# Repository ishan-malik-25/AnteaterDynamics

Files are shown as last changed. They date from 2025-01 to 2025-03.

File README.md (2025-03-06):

# Anteater Dynamics 7DOF Robot Blog

Welcome to our GitHub Page! We are a team of six undergraduate engineers working with our industry sponsor ROBOTIS to develop a 
7-degree-of-freedom robotic arm to be used by robotics enthusiasts and to help in data collection to be used to 
further develop robotics systems. This page will document our team's progress throughout the lifespan of our project
and will include any files, simulations, documents, or other relevant information pertaining to our project.

Team members:

Rogel Aguilar - Mechanical Engineering Major, Software Subteam - https://www.linkedin.com/in/rogelagui/

Diego Avila - Mechanical Engineering Major, Software Subteam

Lucas Cardona - Mechanical Engineering Major, Mechanical Subteam - https://www.linkedin.com/in/lucas-cardona/

Noah Castillo - Mechanical Engineering Major, Electrical Subteam - https://www.linkedin.com/in/noahscastillo/

Ishan Malik - Mechanical Engineering Major, Mechanical Subteam - https://www.linkedin.com/in/ishanmalik1/

Tomas Mejia - Mechanical Engineering Major, Electrical Subteam 

----------------------------------------------------------------------------------------------------------------------------------
Update 3/6/2025 - Mechanical Subteam

This week has been focused on developing a proof of concept to be displayed at our university's winter design review on March 13th. 
For this design review, mainly for the sake of simplicity, and since our software is still being developed, we are splitting the arm assembly
into two separate parts. Both of these components now have updated CAD models and bill of materials that include all of the fasteners
necessary for assembly. We have also obtained all of the actuators and frames from ROBOTIS, and are in the process of 3D printing
all of the necessary components to assemble our proof of concept in the next coming week.

First will be the end effector with the load cells, where focus will be calibrating the load cells and
gaining an understanding of how the torque applied to the servo on the end effector translates to a certain value of gripping force. All parts for the end efffector have been manufactured and are assembled, once the load cells are calibrated we can begin testing this subsystem.



End Effector parts that were manufactured.

Second is the arm linkage, which is simplified into a 4-DOF arm without an end effector, so we can focus on understanding how 
various servo inputs translate into positioning the arm into a desired orientation. Our focus with the linkage arm will be on
repeatability of achieving desired positions, and will include attaching masses to the end of the linkage to analyze how
adding mass affects the accuracy and repeatability of the arm's movement. 



Arm Linkage to be Shown at Design Review, Simplified into 4DOF with Fasteners

As the project progresses into our next academic quarter, the focus will be on fully integrating the entire assembly and making the
system as a whole looks more polished, with shrouds and covers for cables and servo joins similar to those implemented on the 
Open Manipulator X platform.

CAD assembly files of both the proof of concept assemblies will be uploaded to this repository as well as the updated BOMs for these parts.
We have also included a copy of the preliminary testing plan for our proof of concept, which may evolve as we start assembling components.

----------------------------------------------------------------------------------------------------------------------------------
Update 2/27/2025

This week was focused on each of our team members completing an individual component analysis for a part in the robotic arm.
All of these analysis reports are uploaded to this repository to be viewed. These analyses helped justify the design decisions
made in our engineering design process.

Additionally, we made our project poster to be shown at our school's Winter Design Review on March 13th. This poster
summarizes the project and has also been uploaded to this repository.

----------------------------------------------------------------------------------------------------------------------------------

Update 2/20/2025 - Noah

FEA on our custom end effector brackets has been completed. We were discussing manufacturing materials for custom components and had considered either 1060 Aluminum or ABS plastic. The project's intention is to design the robot for at-home manufacturing as well as mass production, and thus want to emphasize additive manufacturing technologies. However, we were concerned that certain connecting components may need a stronger aluminum material to handle the loads. However, the simulation results show that a simple ABS plastic is structurally sound even under a 2X scaled load. In the simulation, the bracket assembly is subjected to a 12 N force acting on the four bracket screw holes. Using aluminum, the maximum displacement is only 0.00063 mm, and for ABS the maximum displacement is 0.022955 mm. Such a small displacement, even using ABS, has proven that using ABS plastic is sufficient for our custom bracket.



Displacement Results of Bracket Assembly using ABS



Displacement Results of Bracket Assembly using 1060 Aluminum

Update 2/20/2025 - Ishan

More progress has been made on the CAD, mainly on the base design - changing it from a simple circular plate to a more realistic
final design. See the picture below. Also finite element analysis (FEA) work has begun to optomize the shape of the linkage arms to
resist bending, I have also attached a few images of FEA results for the original linkage arm cross section seen in the previous
CAD models as well as one for an H-Beam. More shape iterations are currently in progress.


New Base first Revision - Packaging of RB-150 and Base Servo, Holes for Bolting/Clamping


Original Cross Section FEA Displacement with 2N Point Force Applied


H-Beam FEA Displacement Results with 2N Point Force Applied 

----------------------------------------------------------------------------------------------------------------------------------

UPDATE 2/10/2025 - Ishan

More progress has been made on the CAD (RevC) as we are finalizing the selection of the Dynamixel X servos being used in our arm. 
We were having trouble balancing the 7DOF functionality desire with the budget we are targeting and as such have changed some of the
servos used. Previously, all of the servos were from the XM line, but we had to change this to incorporating servos from the 
XC, XM, and XL lines to balance our cost and functionality requirements. We also changed the last servo in the linkage from two
separate servos to a single 2-axis XC-430 servo to save both cost and weight at the end of the linkage. An updated CAD model can
be seen below. The pink servos are XC-430, the green servo is XM-430, the orange is XL-430, and the light blue is the 2-axis 2XL-430.
Additionally, we have uploaded a copy of our project problem definition presentation to the site to be viewed!


Robotic Arm RevC

Dynamixel X Servo Decision Matrix

----------------------------------------------------------------------------------------------------------------------------------
UPDATE 2/4/2025 - Ishan

Progress has been made on the CAD! See the attached photos. The assembly now uses all ROBOTIS actuators and frames.
The servos in the assembly are not specified as they will be in the final assembly as calculations need to be done to ensure
that stall torques are not achieved on any servos. The ROBOTIS form factors for the servos are all ROBOTIS 430 dimensions except for the base 
servo which is 540 dimensions. The overall reach of the arm is now ~655mm, but this can be adjusted by varying the length of the links 
once more robot kinematics are further validated. The arm as shown in the picture has 6 degrees of freedom, with one degree of
freedom reserved for the end effector that is still being developed. Link cross-sections are also yet to be optimized. This
will be done in the coming weeks using FEA once the lengths are more final, so we know what types of forces and moments are 
being experienced by the links on the arm. Note this is Revision B of the CAD; Revision A did exist between the preliminary CAD
and RevB but was mostly used to integrate ROBOTIS servos and frames, while RevB is more representative of our project objectives.



Robotic Arm RevB



Overall Arm Reach at Current Revision

----------------------------------------------------------------------------------------------------------------------------------

1/29/2025



Preliminary Linkage

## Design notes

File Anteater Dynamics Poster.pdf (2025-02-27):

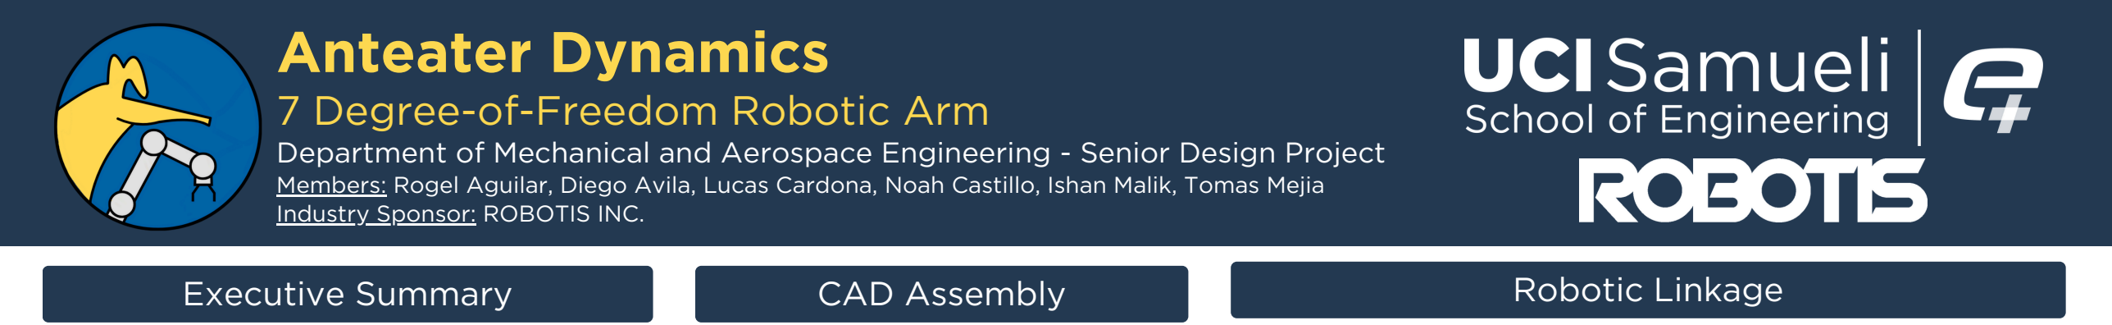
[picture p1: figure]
Robotic Linkage; CAD Assembly; Executive Summary; Anteater Dynamics 7 Degree-of-Freedom Robotic Arm; Industry Sponsor: ROBOTIS INC.
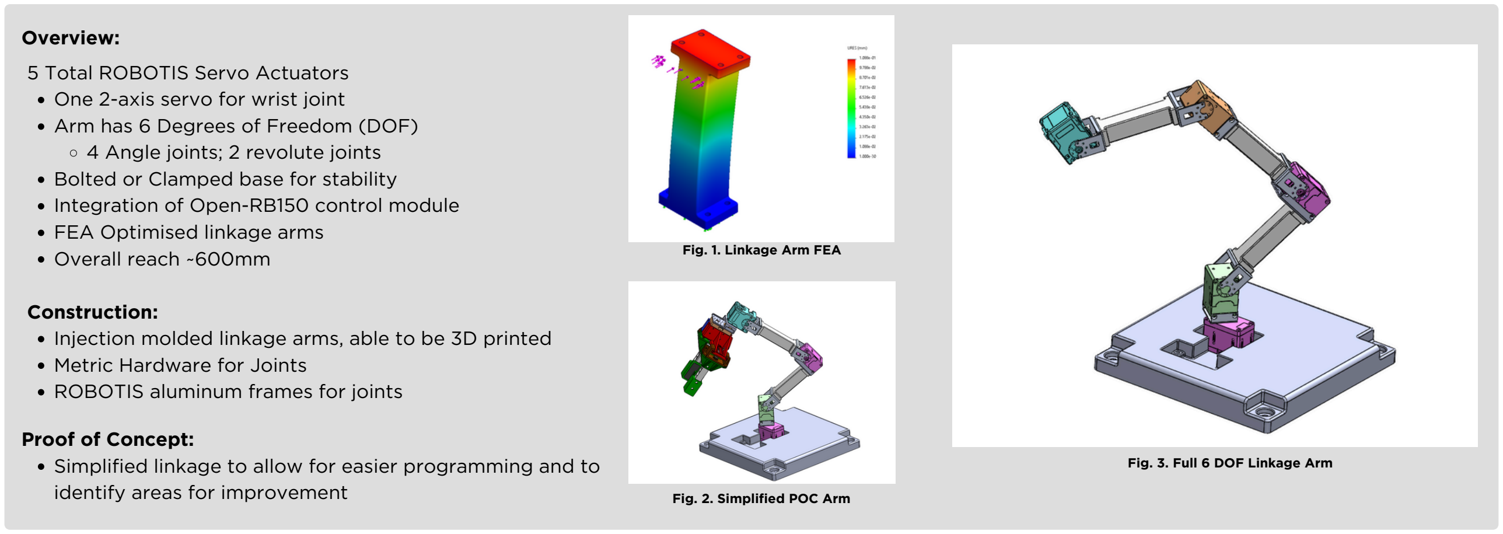
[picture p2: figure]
Overview:; 5 Total ROBOTIS Servo Actuators One 2-axis servo for wrist joint Arm has 6 Degrees of Freedom (DOF) 4 Angle joints; 2 revolute joints Bolted or Clamped base for stability Integration of Open-RB150 control module FEA Optimised linkage arms Overall reach ~600mm; Construction:; Metric Hardware for Joints ROBOTIS aluminum frames for joints; Proof of Concept:; identify areas for improvement; Fig. 1. Linkage Arm FEA; Fig. 2. Simplified POC Arm; Fig. 3. Full 6 DOF Linkage Arm

# End Effector

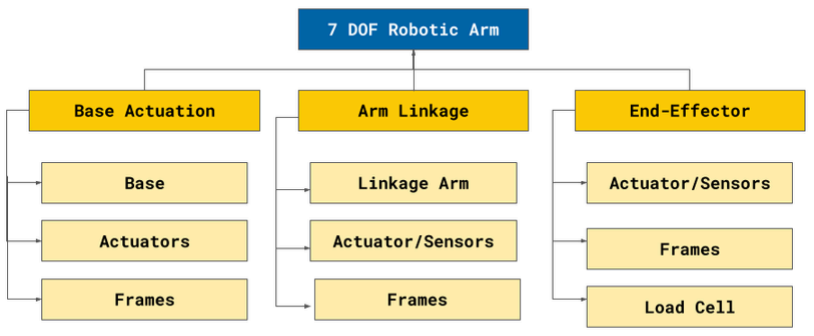
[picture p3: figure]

(A) Base Actuator
FRA-1: The base actuator shall rotate 360 degrees to pick up objects around it
FRA-2 The base shall provide a stable and secure mounting platform for the arm linkage FRA-3 The base shall support the mass of the robot and a load of 400g at the end effector
(B) Arm Linkage
FRB-1: The arm linkage shall provide the reach to pick objects at a distance of 500mm away FRB-2: The servos in the arm linkage shall support the load of 400g at the end effector FRB-3 The arm linkage shall articulate to move around obstructions
(C) End Effector
FRC-1: The end effector shall pick up small household objects
FRC-2: The end effector shall sense gripping forces
FRC-3: The end effector shall be able to grip the expected loads of 400g

# Functional Requirements

The current machine learning research landscape is utilizing robotic systems to collect data on which AI models are trained. Companies such as our industry sponsor, ROBOTIS Inc., provide at-home robotics kits for enthusiasts to collect data and train AI models. The problem is that the available consumer options are either low budget, robot kits with low fidelity or high-end kits that may be unrealistic for many consumers.
Anteater Dynamics seeks to bridge the gap between existing market options by developing a mid-range robotic system capable of 7 degrees of freedom with integrated load sensors to collect critical data for AI training. Our solution is open-source, priced around $1000, and designed for additive manufacturing, allowing consumers to either purchase full kits from ROBOTIS Inc., or opt to manufacture their robot independently from any hobbyist 3D printer. The system is also designed to integrate ROBOTIS Inc. proprietary electronics for optimized linkage kinematics. Simulated kinematic analysis validates unrestricted 7DOF movement and if the 4DOF prototype demonstrates the system effectiveness, the Anteater Dynamics robotic arm could provide the robotics machine learning community with a robust and capable solution for AI training.

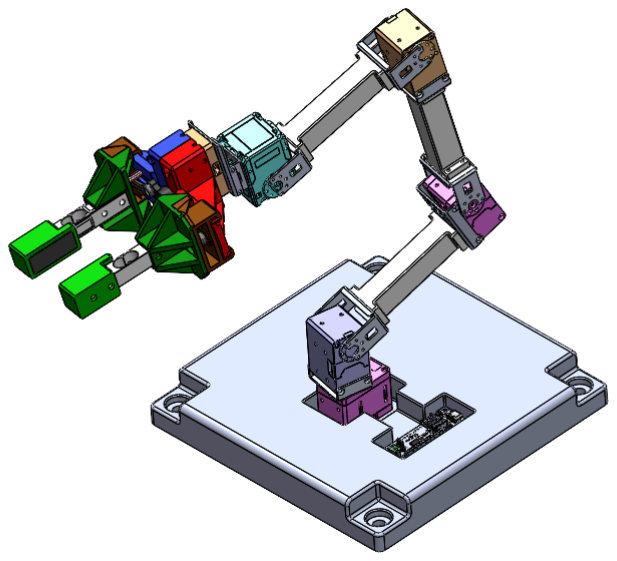
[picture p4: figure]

# Existing Solutions

# Future Improvements

# References and Awknowledgements

Our team would like to thank our sponsor ROBOTIS, for providing feedback and guidance, as well as supplying Anteater Dynamics with DYNAMIXEL servos and other ROBOTIS components. We would also like to thank our MAE151A instructors, Professors David Copp and Mark Walter, and our TA Abdelrahman ElMaradny.

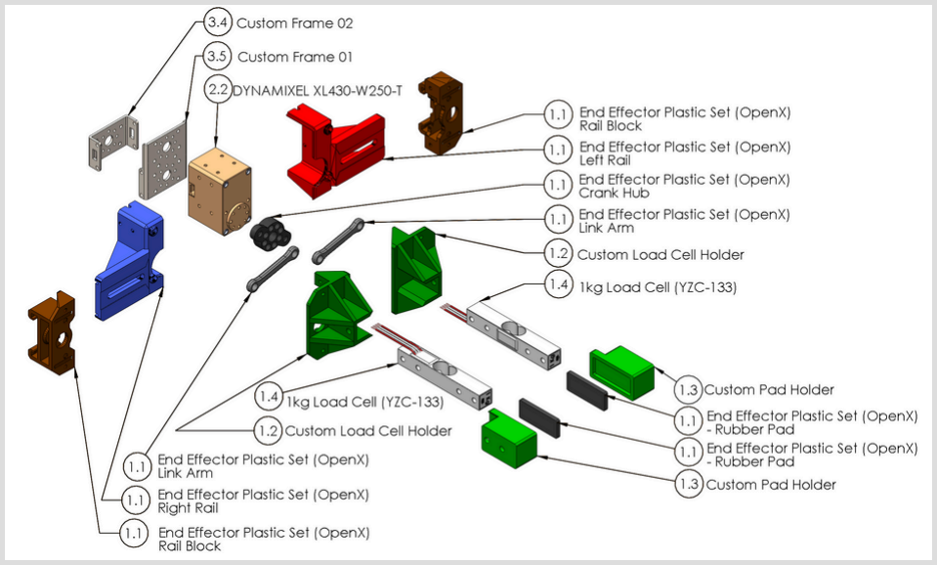
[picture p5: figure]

# Controls/Software

# Structural Decomposition

# Department of Mechanical and Aerospace Engineering - Senior Design Project

Members: Rogel Aguilar, Diego Avila, Lucas Cardona, Noah Castillo, Ishan Malik, Tomas Mejia

O Assembled & Exploded Views: verview: ROBOTIS XL430-W250-T Actuator
- Max Jaw Width; 50.5mm
Construction;
- Injection Molding
- 3D Printing
Active Grip Control;
Each “finger” of the claw is equipped with a 1kg Load Cell. Allowing for machine learning to actively control its applied grip force.
Modularity;
Fingertip pads can be easily swapped for specific
applications.
Fig. 5. End Effector - Assembled View Right Fig 6. End Effector - Exploded View

Fig. 4. End Effector - Assembled View Left

Pseudocode Flowchart

AI Integration and Control

Interchangeable end effectors

Shortcomings | For the Future

Servo Torque Control

Expensive Servos

Torque requirements

Servo Optimization

Complex Control Algorithms

Injection molded linkage arms, able to be 3D printed

Simplified linkage to allow for easier programming and to

Fig 1. Koch v1.1 Robot Arm $237
Low Fidelity
4 DOF

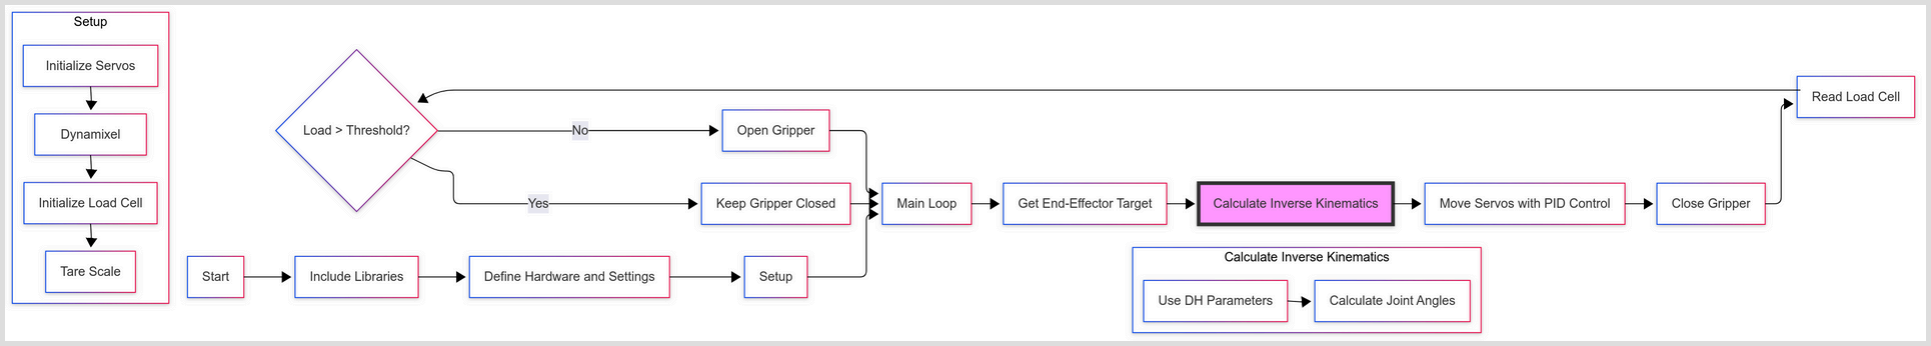
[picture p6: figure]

Fig 7. Flowchart of the Robotic Controls Code

Fig 2. OpenManipulator-X Robot Arm $1,416
High Fidelity
6DOF

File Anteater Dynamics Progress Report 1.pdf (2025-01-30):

# Anteater Dynamics 7 DOF Robot

01/23/2025 - 01/30/2025

Rogel Aguilar, Diego Avila, Lucas Cardona, Noah Castillo, Ishan Malik, Tomas Mejia
University of California, Irvine Henry Samueli School of Engineering

# Summary

Over this past week, Anteater Dynamics primarily focused on operational tasks. The team developed a contract that our members are meant to follow over the project lifespan. The team is currently working on problem definition, gaining an understanding of what specific components and needs must be integrated into the system. Additionally, a basic linkage design was created in Solidworks, validating the number of degrees of freedom and getting a basic understanding of the kinematics of the robotic arm.

https://github.com/ishan-malik-25/AnteaterDynamics

# Goals

Goal 1: Kinematic validation of robotic arm with 7DOF

Goal 2: Developed problem definition for project objectives

# Outcomes

Goal 1: Kinematics Validation

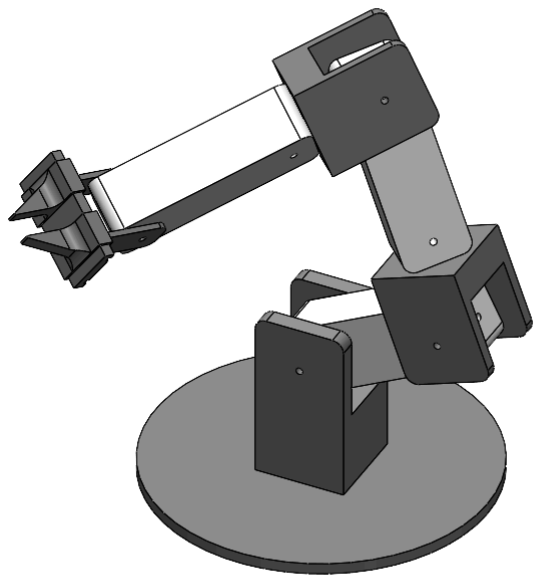
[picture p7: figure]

- Kinematics mock-up of 7DOF robotic arm in Solidworks

Goal 2: Problem Definition

Problem Defenition (https://docs.google.com/presentation/d/1wHaiUMOAIBBrATz0K1sZ1rZ3FSAhI8pwVjJIr-QNW-A/edit?usp=sharing)
- Problem Definition presentation is in progress

# Moving Forward

Plans before the next reporting period include refining and performing simulations to verify our kinematic outline further. The Mechanical sub-team will take the lead in the outline, while the other team members will provide support and feedback.

The electrical team will continue to finalize the actuators and other components needed to transition from modeling and simulation to physical prototyping.

The software team will begin to set deadlines and objectives to familiarize themselves with the ROS and Gazebo software environment.

We anticipate encountering challenges in any initial simulations especially as we continue to refine and clarify our design requirements and needs. The concept generation stage for our kinematic outline will require a lot of back-and-forth between the teams so we need to take into consideration the time needed to spend on the project.

# Time Tracking

1/24 (3 hours, ALL)--Completing Sponsorship Interview Summary
Teammates collaborated on summarizing key takeaways from the initial sponsor interview last Thursday

1/27 (1.5 hours, ALL)--Completing Team Contract
Teammates collaborated on establishing norms on how the team will function going forward. An organizational chart was established and individual design roles were assigned.

1/28 (1.5 hours, ALL)--Existing Solution Research and Preliminary BOM prep
During our lab time, we explored existing robotic arms to start thinking about how we could approach the problem. Additionally, system needs and requirements started to be brainstormed

1/29 (1.5 hours, ALL )--Problem Definition, Timeline creation, Public Documentation During our lab time, more work was done on our problem definition. A Gantt Chart was started to track the team’s group and individual tracks. The type of public documentation was decided, and a GitHub Page was created

1/29 (2 hours, Ishan)--Preliminary Linkage CAD
Preliminary design of our CAD model was developed by Ishan with input from the team.

Link to Gantt Chart (https://docs.google.com/spreadsheets/d/15tDmBBRLZHagoX_M0EPwx-CAiR3B7cbavoiCkAHe7NM/edit?usp=sharing)
Link to GitHub (https://github.com/ishan-malik-25/AnteaterDynamics)

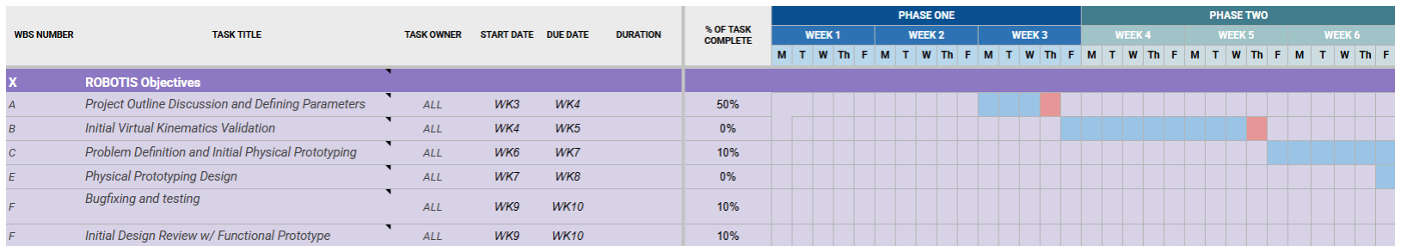
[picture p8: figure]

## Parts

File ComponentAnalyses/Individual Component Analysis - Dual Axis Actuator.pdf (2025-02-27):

Individual Component Analysis – Dual Axis Actuator

Project Description

This project’s objective is to design and manufacture a robotic arm with seven degrees of freedom. The goal is to give consumers a more affordable yet quality robot arm that can be utilized to collect data for machine learning and artificial intelligence.

Analyzed Component: DYNAMIXEL 2XL430-W250-T

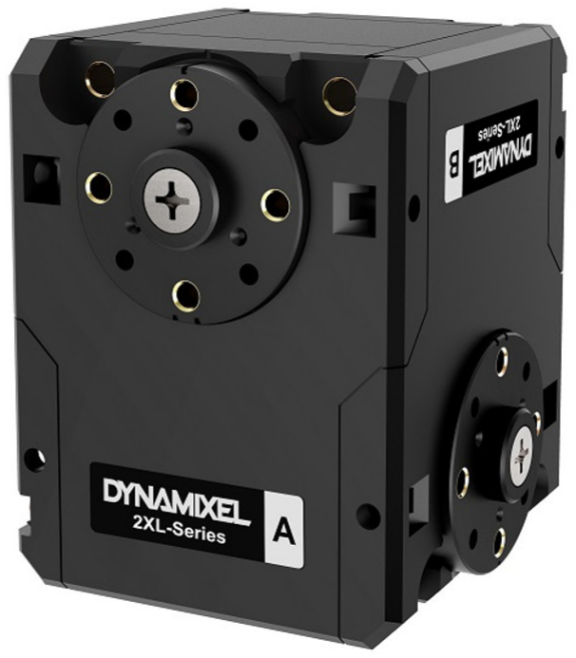
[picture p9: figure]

Figure 1: DYNAMIXEL 2XL430-W250-T
The component that will be analyzed in this write-up is the DYNAMIXEL 2XL430-W250-T, a dual axis actuator sold by Robotis. This component is critical to the design because it serves as the connection between the robot’s arm linkage and end effector. It also provides an additional two axes giving the end effector a wider range of mobility and flexibility.

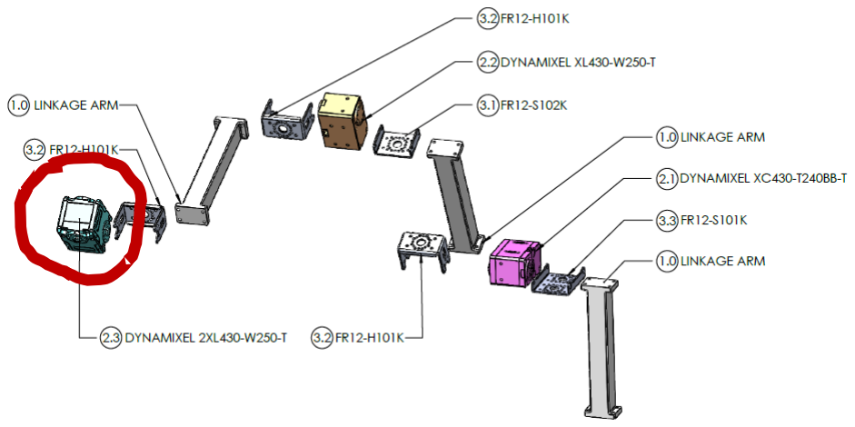
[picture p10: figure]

Figure 2: The DYNAMIXEL 2XL430-W250-T is the final component on the arm linkage and is what is used to join it and the end effector
Functional Requirements
Requirement Code | Requirement
FR-001 | The actuator shall be capable of supporting the end effector
FR-002 | The actuator shall be capable of lifting a load of 500 grams when grabbed by the end effector
FR-003 | The actuator shall be dual axis or utilize two actuators for two degrees of freedom

Component Options

The project’s sponsor set a requirement that all actuators were to be Robotis brand. This meant options were limited to their catalogue. The following is a short description of three alternate options to the DYNAMIXEL 2XL430-W250-T.

DYNAMIXEL 2XC430-W250-T:

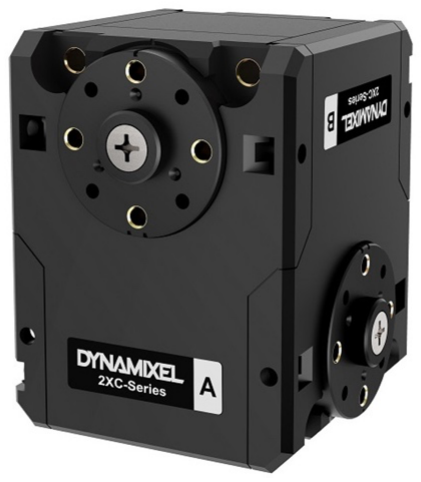
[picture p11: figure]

The 2XC430-W250-T is a dual axis actuator with a 1.8nm stall torque.

DYNAMIXEL XL430-W250-T:

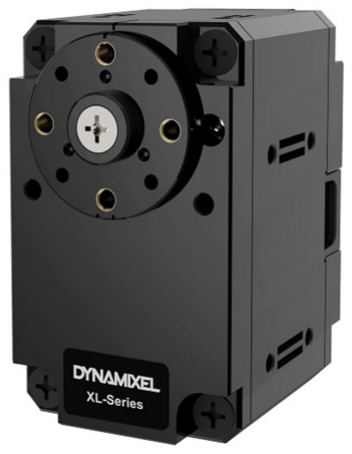
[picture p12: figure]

The XL430-W250-T is a single axis actuator with a 1.4nm stall torque. Two in junction are required to achieve an equivalent number of degrees of freedom.

DYNAMIXEL XL330-M288-T:

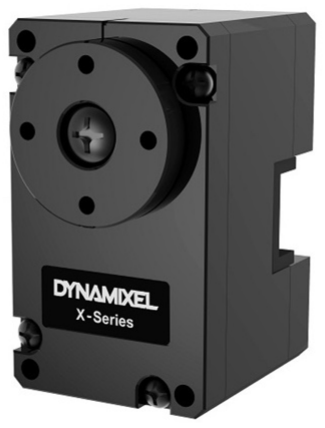
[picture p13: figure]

The XL330-M288-T is a single axis actuator with a 0.52nm stall torque. Two in junction are required to achieve an equivalent number of degrees of freedom

Summary Table

Component Name | Cost | Pros | Cons
2XL430-W250-T. | $129.90 | • Dual Axis • Inexpensive • Good torque • Metal Gears | • Large
2XC430-W250-T | $259.90 | • Dual Axis • High torque • Metal gears | • Large • Expensive
XL430-W250-T | $49.90 | • Inexpensive • Good torque | • Single Axis • Plastic gears
XL330-M288-T | $23.90 | • Inexpensive • Small and light | • Single Axis • Low torque • 5V input

Component Justification

The reason for selecting the 2XL430-W250-T is primarily for its dual axis operation, cost and for having a good stall torque.

Dual axis capabilities play a big role for the actuator selection. It is desirable to have two axes for the end effector because it gives it additional movement and rotation for it to pick up objects. Besides the 2XL430-W250-T, the 2XC430-W250-T is the only other dual axis actuator that Robotis sells. It has a stronger motor with a stall torque of 1.8nm over the 1.4nm of the 2XL. The major drawback to it, however, is that it is double the cost. Additionally, the XC series of actuators are praised for their more durable metal gears, however, the 2XL is also equipped with metal gears. The twice as large price tag is unjustifiable because its only standout attribute over the 2XL is its higher stall torque. Because this actuator is placed right before the end effector, the moment on the motors is not as large, especially compared to those closer to the base, so the additional torque isn’t weighted as strongly. For the alternate single axis options, to achieve the save mobility as the dual axis, two actuators connected are required. This adds additional complexity and cost for required hardware. In addition, the total weight and size of two actuators generates a larger moment for the actuators at the base.

As stated before, the cost of the 2XC is unjustifiable for the little benefits it provides. The XL430 and XL330 are both cheaper options but requiring two doubles their cost. Using two motors, the XL330 still shows to be an affordable option. Looking deeper at its low stall torque of 0.52nm, it is roughly a third of the stall torque the 2XL, making it a less competitive option. Doing rough calculations, the motor needs at least 1nm of torque to fulfill the lifting capacity of 500grams for the project. The 2XC capable of 1.5nm of torque surpasses this target making it the clear choice of actuator.

Specifications

Weight: 98.2g

No-load RPM: 57 RPM

Dimensions: 36x46.5x36mm

Resolution: 4096 steps

Voltage Input: 11.1V

Stall Current

Stall Torque

Gear Ratio: 257.4:1

Dual Axis

References

Sutyasadi, Petrus. Control Improvement of Low-Cost Cast Aluminium Robotic ..., repository.usd.ac.id/45285/1/9057_11+Control+Improvement+of+Low-Cost+Cast+Aluminium+Robotic+Arm+Using+Arduino+Based+Computed+Torque+Contr ol.pdf. Accessed 8 Dec. 2022.

2XL430-W250 ..., https://emanual.robotis.com/docs/en/dxl/x/2xl430-w250/

2XC430-W250 ..., https://emanual.robotis.com/docs/en/dxc/x/2xc430-w250/

XL430-W250 ..., https://emanual.robotis.com/docs/en/dxl/x/xl430-w250/

XL330-M288-T ..., https://emanual.robotis.com/docs/en/dxl/x/xl330-m288/

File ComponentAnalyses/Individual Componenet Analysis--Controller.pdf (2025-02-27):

# Individual Component Analysis: Controller

## 1. Project Description and Individual Component Justification

Anteater Dynamics is working on a low-cost 7 degree-of-freedom robotic arm using proprietary components supplied by the team’s industry sponsor ROBOTIS Inc. The motivation behind the project was for hobbyists and robotics enthusiasts to have a middle ground between low-fidelity budget options and cost prohibitive high-fidelity options. One of the main requirements for this project is to keep the total cost under $1000. Below is a grey box diagram of the major functions the robotic system aims to achieve.

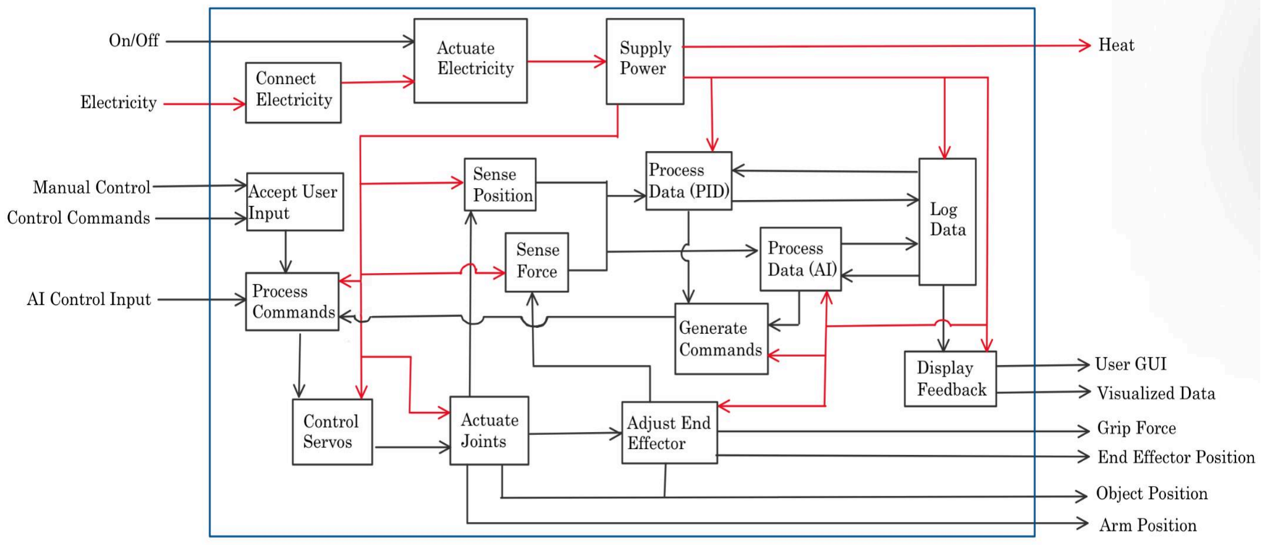
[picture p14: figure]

Fig 1. Grey Box Diagram of the Robotic Arm [1] The controller plays in integral role as this component will receive the manual control and control commands from the user, and process those commands to help achieve the final end effector position through mathematical computation (inverse kinematics), adjust the grip force of the end effector by reading load cell data, as well as displaying data through a GUI. The type of controller is critical as it needs to be able to handle executing all the different functions described in the grey box diagram shown above.

## 2. Functional Requirements and Other Considerations

The functional requirements of the robotic controller are as follows:
FR-Cr1: The controller shall control six servos at once
FR-Cr2: The controller shall be able to perform mathematical calculations such as forward or inverse kinematics
FR-Cr3: The controller shall process input data from the load cells

While not necessarily requirements there are other considerations and suggestions that should be taken into account. The end-product is aimed toward hobbyists and other robotic enthusiasts as well as researchers. With this broad end-user audience, the controller should be relatively simple to use, or should not have too high of a learning curve. Additionally, cost shall be considered when choosing a controller as the main goal of this project is to keep the final product price to be under $1000.

## 3. Concepts or Options

From the DYNAMIXEL quick start manual and selection guide, the DYNAMIXEL servos can be controlled three ways, by an Arduino-compatible microcontroller, a single-board computer (SBC), or directly from a PC. [2, 3] For this component the three options will be
1. A generic Windows or macOS laptop with at least 8 GB of RAM.
2. A Raspberry Pi 4 Model B (2 GB RAM) SBC.
3. The OpenRB-150 controller.

For direct PC control, the specifications for the PC will be based on the Lenovo IdeaPad Slim 3i 15.6" available at Costco [4]. This is a newer generation of a laptop currently used by a project member and can operate a variety of different applications including WSL, SolidWorks, and MATLAB. Control of the DYNAMIXEL servos can be achieved via the DYNAMIXEL Software Development Kit (SDK) which allows the DYNAMIXEL to be programmed in several different languages. A diagram of how the PC is connected to the DYNAMIXEL is shown in the figure below.

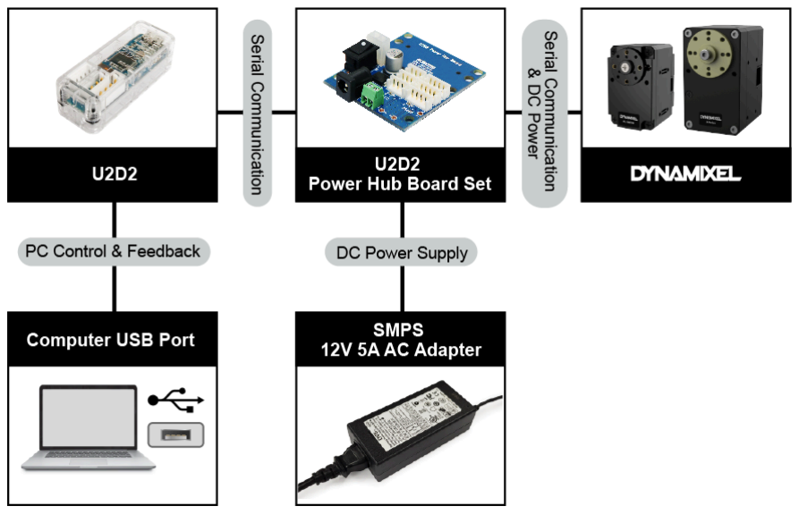
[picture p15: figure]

Figure 2. Flowchart highlighting how a PC is connected to the the DYNAMIXEL servos [3]

As seen in the figure, three additional components are necessary for communication between the PC and the servos. The U2D2 converts USB to either TTL and/or RS-485, depending on which model servo is being used. The U2D2 power hub is what connects directly to the DYNAMIXEL and is connected to an external power source.

The Raspberry Pi 4 Model B is an SBC that runs on the Linux operating system. Similar to direct control from a PC, the Raspberry Pi can program the DYNAMIXEL through the Dynamixel SDK, and the flowchart shown in Figure 2. But instead of a Computer USB port, the Raspberry Pi USB port will be used.

Lastly, the OpenRB-150 is an Arduino-compatible microcontroller designed and sold by ROBOTIS. Control of the DYNAMIXEL servos can be achieved through the Arduino IDE and the Dynamixel Arduino library.

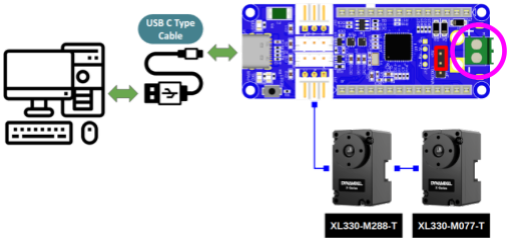
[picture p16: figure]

Fig 3. Diagram of OpenRB-150 Connection [3] As shown in figure above, the OpenRB-150 is the only component needed to control the robotic arm. Note that the OpenRB-150 can be powered through an external source via the pins circled in bright pink. This functionality is needed when using more powerful servos.

## 4. Pros and Cons Summary

Below is a table representing a summary of the pros and cons of the three different options:

Component | Pros | Cons
Direct PC | Most Versatile | High learning curve
| Highest Computing Capacity | Not Beginner Friendly
Raspberry Pi | Portable | Most Costly Solution
| Strong computing capability | Not beginner friendly

Limited Versatility compared to PC

OpenRB-150 | Arduino-compatible (beginner friendly) | Small memory/Weak computing power
| Cheapest Option | Only 4 TTL Ports

Only uses TTL ports

Highlighted in green is the chosen component. Further analysis how this decision was made will be discussed in the following section

## 5. Analysis and Justification

Rating 1-5 | Robotic Arm Controller
Direct PC | Raspberry Pi 4 B | OpenRB-150
Objectives | WEIGHT | Rating | Weighted Score | Rating | Weighted Score | Rating | Weighted Score
Cost | 40.00% | 3.00 | 24.00% | 1.00 | 8.00% | 5.00 | 40.00%
Computing Power | 30.00% | 5.00 | 30.00% | 4.00 | 24.00% | 1.00 | 6.00%
Compatibility/ Versatility | 15.00% | 5.00 | 15.00% | 3.00 | 9.00% | 1.00 | 3.00%
Ease of use | 15.00% | 3.00 | 9.00% | 2.00 | 6.00% | 4.00 | 12.00%
SCORES | 100.00% | 3.90 | 78.00% | 2.35 | 47.00% | 3.05 | 61.00%

The objectives listed in the weighted decision matrix relate to the functional requirements and other considerations discussed in section 2 of this paper. Important to note, an assumption was made that the end-user will already have a PC with similar or better specifications as the Lenovo laptop used in this analysis.
Cost is weighted as the most important factor as the goal of the project is to have a low-cost option for consumers. The OpenRB-150 gets the highest rate in this category, with a single board costing only $24.90. [5] The runner up is the direct PC control–under the assumption the user already has a PC similar in specifications to a Lenovo laptop–as the U2D2 starter pack costs $59.70 [6]. Under this assumption the direct PC controller received the rating of 3, since the cost of this method will only be the U2D2 and its accompanying Power Hub Board. The Raspberry Pi is the costliest option with an additional $44.99 for the SBC itself on top of the $59.70 cost of the U2D2 starter set [7]
Computing power is the second highest-weighted category. All the functional requirements require ample computing power and the direct control of the PC provides sufficient computing power to perform more resource intensive tasks such as calculating the proper thetas for rotation with inverse kinematics, or getting the final position of the end effector with forward kinematics. The Raspberry Pi 4 is the second highest-rated in computing power technology. As an SBC, the Raspberry Pi has a CPU which can process more data than an Arduino [8].
The next two categories carry the same weight, compatibility/versatility and ease of use. Compatibility and versatility is related to which languages and programming environments can be used in the controller. Again the PC had the highest rating since it can use all the languages supported by the Dynamixel SDK (C, C++, C-Sharp, Python, Java, Matlab, Labview, and ROS). [2, 3] While the Raspberry Pi 4 is able to use these languages as well, compatibility is limited for example, since MATLAB cannot be directly installed on and run on a Raspberry Pi. [9] Ease of use relates to how beginner friendly each controller is. While not a functional requirement, it’s important to consider given the large end-user audience. The OpenRb-150 has the highest rating here since the DYNAMIXEL can only be used in the ArduinoIDE environment along with the Arduino2Dynamixel library. These limitations help beginners code basic commands to the DYNAMIXEL servos.

## Specifications for Chosen Component

From the Decision Matrix, direct PC control is the chosen method for controlling the robot. The specifications for this component will be focused on the U2D2 and U2D2 Power Hub Interface devices.

The U2D2 connects to the PC via a USB Type-A cable. The ports on the U2D2 include a 3 Pin TTL and a 4 PIN RS-485, both for connecting to DYNAMIXEL. The last port is a 4 Pin UART. The maximum baud rate is 6 Mbps. [9]

The U2D2 Power hub has 3 TTL ports and 3 RS-485 to connect to the DYNAMIXEL servos. The U2D2 power hub has an operating voltage of between 3.5V and 24.0 V, with a max current of 10.0A.

## References and Notes

[1] Cardona, L., "Problem Definition," MAE 151A, PowerPoint presentation, Irvine, CA, Feb. 4, 2025. Slide 11
[2] “DYNAMIXEL Selection Guide,” ROBOTIS e-Manual, Mar. 24, 2024. https://emanual.robotis.com/docs/en/reference/dxl-selection-guide/#controller--interface (accessed Feb. 27, 2025).
[2] “DYNAMIXEL Quick Start Guide,” ROBOTIS e-manual, 2025. https://emanual.robotis.com/docs/en/dxl/dxl-quick-start-guide/ (accessed Feb. 27, 2025).
[3] “Lenovo IdeaPad Slim 3i 15.6" Touchscreen Laptop - Intel Core 5 120U - 1080p - Windows 11,” Costco Wholesale, 2022. https://www.costco.com/lenovo-ideapad-slim-3i-156-touchscreen-laptop---intel-core-5-120u---10 80p---windows-11.product.4000260119.html (accessed Feb. 27, 2025).
[4] “OpenRB-150,” ROBOTIS, 2025. https://www.robotis.us/openrb-150/ (accessed Feb. 27, 2025).
[5] “DYNAMIXEL Starter Set [US],” ROBOTIS, 2025. https://www.robotis.us/dynamixel-starter-set-us/ (accessed Feb. 27, 2025).
[6] “Raspberry Pi 4 Model B - 2GB DDR4,” Micro Center. https://www.microcenter.com/product/621439/raspberry-pi-4-model-b---2gb-ddr4?src=raspberry pi
[7] J. Cicolani and Springerlink (Online Service, Beginning Robotics with Raspberry Pi and Arduino : Using Python and OpenCV. Berkeley, Ca: Apress, 2018. Available: https://learning.oreilly.com/library/view/beginning-robotics-with/9781484268919/
[8] “Raspberry Pi,” Mathworks.com, 2024. https://www.mathworks.com/hardware-support/raspberry-pi.html (accessed Feb. 27, 2025).
[9] Y. Name, “U2D2,” ROBOTIS e-Manual. https://emanual.robotis.com/docs/en/parts/interface/u2d2/
[10] Y. Name, “U2D2 Power Hub,” ROBOTIS e-Manual. https://emanual.robotis.com/docs/en/parts/interface/u2d2_power_hub/

DYNAMIXEL Selection Guide (https://emanual.robotis.com/docs/en/reference/dxl-selection-guide/#controller--interface)
Direct PC/SBC:
- Requires U2D2
- Converts USB to TTL/RS-485 Signal
- Then the U2D2 Power Hub Board Set
- This also applies to when using the Raspberry Pi
- Power Supply

OpenRB-150:
- Needs an arduino or for our case OpenRB-150
- Power Supply

- Arduino IDE
- 4 TTL connectors

Software Tools:
- Dynamixel Wizard 2.0
- Works on both u2d2 and OpenRB [Source] (https://emanual.robotis.com/docs/en/parts/controller/openrb-150/)
- Dynamixel SDK (software development kit)
- Supports a lot of different languages
- Available on all three major OS (Linux, macOS, Windows
- Arduino Library
- ROBOTIS has library to make coding in arduino ide easier

DYNAMIXEL SDK Guide: (https://emanual.robotis.com/docs/en/software/dynamixel/dynamixel_sdk/overview/)
- Can be used for both PCs and SBC
- Can use these languages: C, C++, C#, Python, Java, MATLAB and LabVIEW

Costs (based on the ROBOTIS Website)

Direct PC:
- U2D2 starter set (https://www.robotis.us/dynamixel-starter-set-us/) is $59.70
- This will be the only cost for direct PC control
- If you do a la carte the u2d2 will cost 32.10
- The power hub will be 19.00
- 51.10 if bought a la carte

Raspberry Pi 4 Model B:
- U2D2 and then on top of that the actual raspberry pi
- From Micro-center (https://www.microcenter.com/product/621439/raspberry-pi-4-model-b---2gb-ddr4?src=raspberrypi) it will cost 44.99

OpenRB-150 (https://www.robotis.us/openrb-150/)
- Open RB itself will cost $24.90
Specs:
- 256 KB Flash Memory
- 32 KB SRAM

Can take both power from PC or external power supply

Quick pros and cons
OpenRB-150 is the CHEAPEST Option (Maybe put this in a decision matrix) OpenRB-150 is also most limiting since it can only be coded in arduino IDE

Raspberry pi:
More powerful than openrb-150 when it comes to computing (has better specs) Most Costly, assuming user has access to a laptop

PC:
Most versatility, can use a variety of different software programming tools
Least portable of the three. Potentially limiting as well if people don’t have access to a PC (say they only have a chromebook)

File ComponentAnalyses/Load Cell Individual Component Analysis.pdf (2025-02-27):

Lucas Cardona
Professor Walter
ENGRMAE 151A
Feb. 26, 2025
Individual Component Analysis; Load Cell
Description:
The 7 Degree of Freedom (7 DoF) Robotic Arm must be able to receive feedback data in regards to how much grip force it is applying at the end effector. Therefore, the design must include some sensor with the ability to detect the applied force on the object. This verifies a need for selecting an appropriate type of sensor and for this design a bar load cell was chosen. The bar style load cell is advantageous to the design as it can function as part of the “fingers” saving on the amount of needed plastic for injection molding. This being considered, the main requirements for the load cell are that it must be able to withstand the forces needed for holding a 400g object, have an overall length exceeding 45mm, and have an accuracy of +/- 0.1g or better.

Essential Qualities of Load Cells:
- Force sensing:
- Ensuring the robotic arm applies the correct force when grasping objects.
- Closed-loop control:
- Enabling feedback mechanisms for improved accuracy and responsiveness.
- Safety compliance:
- Preventing overloading or excessive force application that could damage components or objects.

Functional Requirements:
Label | Description | Justification
FR-3.1 | Withstand the force of holding a 400g object. | Being able to hold up and manipulate a 500g object is a requirement of our project. Therefore the load cell must be able to withstand the force necessary to do this.
FR-3.2 | Overall length at or exceeding 45mm | The original grippers of a previous ROBOTIS design are near 50mm, in order for the plastic savings to be advantageous the load cell must make up most of this distance.
FR-3.3 | Accuracy of +/-0.1g or better | In order for the feedback system to function the machine learning algorithm must be given accurate data. This will improve the overall performance of the end effector as well as allow a wider variety of objects to be manipulated.

Selected Options:
500G Load Cell (TAL221): | 1kg Load Cell (YZC-133): | 5kg Load Cell (YZC-133):


Overview: | Overview: | Overview:
- Length: 45mm | - Length: 80mm | - Length: 80mm
- Overload Capacity: 1000g | - Overload Capacity: 1500g | - Overload Capacity: 7500g
- Accuracy: 0.7 +/- 0.15 mV/V | - Accuracy: 1.0 +/- 0.15 mV/V | - Accuracy: 1.0 +/- 0.15 mV/V

All 3 options of the compared load cells use strain gauges to measure deformation in the bar. This specific method of measuring applied force is advantageous for our application because they offer high precision and reliability when compared to other options. These are essential qualities for ensuring our end effector can precisely know how much force it is applying and understand the object it is holding. Additionally, strain gauge load cells are very cost-effective allowing our project to remain under budget and be cheap to service. Different bar style load cells were also selected because much of the intended length for the end effectors claws will come from the body of the cell. A few drawbacks of these specific types of load cells are that they require amplification and can be susceptible to temperature variation. In our application temperature variation will not be much of a concern as the working environment will be a desktop. The need for an additional amplifier will affect our overall budget, however they are also cost-effective (~$10/piece).

Weighted Component Matrix:


Summary Table:
Component | Price | Pros | Cons
1kg Bar Load Cell (YZC-133) | $4.99 per unit | - 80mm in length - Appropriate range for application | - Lower safe overload percentage
5kg Bar Load Cell (YZC-133) | $4.99 per unit | - 80mm in length - Wide range of measurement | - Low accuracy - Lower safe overload percentage
500g Load Cell (TAL221) | $11.25 per unit | - Higher safe overload percentage - 150% Rated Load | - Sub-par length - Smaller range of outputted voltage

Analysis:
To ensure that the load cell is capable of handling the forces necessary for holding up a 400g object the following calculations were performed. A free body diagram shows 125% the mass target being held up by the friction forces of the object from the rubber pads of the end effector. To calculate the applied force necessary, first the force of friction was calculated based upon the static loading in the vertical direction. Next to ensure that the frictional force was sufficient to hold the object, an assumption of rubber on plastic for the coefficient of friction was used to find the necessary force to apply at the end effector. This force value was then converted to kilograms to ensure that the cell has enough range to handle the application.


Factor of Safety:
To allow the arm to grip objects with enough force to manipulate them without slipping a factor of safety of over 2 was chosen to ensure this. Given the necessary 0.37 kg the cells needs to withstand, a 1kg load cell is able to offer a factor of safety over 2 with enough fidelity for our system.

Factor of Safety =

Max Load
Designed Load

FOS =

0.5kg
0.37kg = 1. 35 | FOS =

1.0kg
0.37kg = 2. 70 | FOS =

5.0kg
0.37kg = 13. 5

Justification for the Chosen Load Cell:
Based on the analysis above, the 1kg strain gauge-based load cell was selected for use in the end effector of the robotic arm. The main factor for this decision are its;
- Proven reliability in industrial applications.
- Cost-effectiveness compared to other options (piezoelectric; capacitive).
- High accuracy.
- Easy integration.
- Ability to handle a wide range of forces within our specifications.

Chosen Component Specifications:


1kg Load Cell (YZC-133)

Specification | Value
Rated Output: | 1.0 ± 0.15 mV/V
Nonlinearity: | 0.0005
Repeatability: | 0.0003
Hysteresis: | 0.0003


Creep(5Min): | 0.001
Temperature Effect On Sensitivity: | 0.003% RO/°C
Temperature Effect On Zero: | 0.02% RO/°C
Zero Balance: | ± 0.1% RO
Input Resistance: | 1066 ± 20Ω
Output Resistance: | 1000 ± 20Ω
Insulation Resistance: | 2000MΩ (50V)
Recommended Excitation Voltage: | 5V
Compensated Temperature Voltage: | -10 ~+ 50 °C
Operating Temperature Range: | -20 ~+65 °C
Safe Overload: | 120% RO
Ultimate Overload: | 150% RO
Load Cell Material: | Aluminium
Connecting Cable: | 0.8 X 180 mm

References

Sparkfun. (n.d.). Tal221 miniature load cell. 500g Load Cell Data Sheet. https://cdn.sparkfun.com/assets/9/9/a/f/3/TAL221.pdf

Geekstory Digital Load Cell Weight Sensor 1kg High Precision Miniature Load Cells YZC-133 for

Arduino DIY Electronic Portable Kitchen Scale Sensors(Pack of 2): Amazon.com: Industrial &

Scientific. (2025). Amazon.com.

https://www.amazon.com/Geekstory-Digital-Load-Weight-Sensor/dp/B0CJYC7L92?th=1

Hastawan, A. F., Haryono, S., Utomo, A. B., Hangga, A., Setiyawan, A., Septiana, R., Hafidz, C. M., &

Triantino, S. B. (2021). Comparison of testing load cell sensor data sampling method based on the

variation of time delay. IOP Conference Series: Earth and Environmental Science, 700(1), 012018.

https://doi.org/10.1088/1755-1315/700/1/012018

The Ultimate Showdown: Load Cell Comparison Demystified. (2025). Dubai Sensor.

https://www.dubai-sensor.com/blog/the-ultimate-showdown-load-cell-comparison-demystified/

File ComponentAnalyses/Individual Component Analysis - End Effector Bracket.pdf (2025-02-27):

Noah Castillo

Group 13

26 February 2025

Anteater Dynamics - 7DOF Robotic Arm

Individual Component Analysis - End Effector Wrist Brackets


Fig 1. End Effector Wrist Brackets Solidworks Model

The current machine learning research landscape is utilizing robotic systems to collect

data on which AI models are trained. Companies such as our industry sponsor, ROBOTIS Inc.,

provide at-home robotics kits for enthusiasts to collect data and train AI models. Anteater

Dynamics seeks to bridge the gap between existing market options by developing a mid-range

robotic system integrating Robotis Inc electronics that is capable of 7 degrees of freedom with

integrated load sensors to collect critical data for AI training.

One component critical to the success of the overall design is a pair of custom wrist

brackets that the team has designed to enable end effector rotation about two perpendicular axis.

The brackets are designed to join two servos, rotating perpendicular to one another, and thereby

connect the end effector to the robot linkage. While the component structure is dictated by the

fastener requirements of the respective servos, this individual analysis serves to evaluate

different material options for manufacturing this custom component. Unlike other off-the-shelf

brackets incorporated in this design, this bracket is unique to the Anteater Dynamics Robotic

Arm and must be specifically manufactured for this use case. As a result, this analysis will

analyze three potential materials, ABS plastic, 5052 Aluminum, and 6061 Aluminum, through

material property comparisons and stress and displacement static FEA analysis. The results of

this study will inform the team on the viability of additive manufacturing methods and guide

future manufacturing of the robotic arm for retail deployment.

The wrist brackets must be manufactured out of a material that is capable of meeting the

following functional requirements.

1) The wrist brackets shall be capable of holding the end effector assembly and 400g object

without plastic deformation or significant deflection

2) The wrist bracket material shall be capable of supporting threaded screws supporting the

two servo motors for extended use periods without deterioration.

3) The wrist bracket shall not experience stresses exceeding the yield stress of the chosen

material under maximum load with a 400g object given a load safety factor of 2.

Material | Yield Stress (MPa) | Modulus of Elasticity (GPa) | Density (g/cc) | Material Cost
ABS Plastic | 13.0 - 65.0 | 1.00 - 2.65 | 1.01 - 1.20 | $0.01
5052-H32 Aluminum | 193 | 70.3 GPa | 2.68 | $0.57
6061 Aluminum | 276 | 68.9 | 2.70 | $0.61

Fig 2. Table Comparing Material Properties and Costs of Potential Materials

- Material properties sourced from MatWeb (Ref1-3)
- Aluminum priced using (Ref-4) per 12”x12” sheet assuming 20 parts cut per sheet
- ABS plastic priced by 4.88g mass (Ref-5)

The table above displays the relevant material properties and material costs per unit (not

including labor or machining costs for aluminum) for the three material options. ABS plastic

provides a substantial reduction in price when manufactured at scale, and aligns with the larger

goal of Anteater Dynamics to provide a robotic arm solution that is available for open source

manufacturing. Unlike with aluminum, consumers can create the 3D printed brackets at home

without needing a storefront vendor. However, with this advantage comes a significant loss in

material yield strength. To determine if ABS plastic is sufficient to meet the functional

requirements of the wrist bracket, a static finite element analysis study is conducted to analyze

stress and deformation under load.

The load acting on the custom end effector brackets is the weight of the end effector,

including the dual XL-430 servo motor, load cells, and custom manufactured parts. The servo

motor weight is defined on the supplier website to be 45.36g. The remaining weight is

determined using Solidworks mass properties evaluation. The load cells and servo hub are

defined as 1060 Al and all other custom parts are defined as ABS plastic.


Fig 3. End Effector (without servo) with applied materials for mass evaluation

- End Effector Total Mass: 217.03 g
- Max Object Mass: 400g

Load Case: 12.098 N

- Load with 400g object
- Load factor of 2
- ¼ bearing load applied at four screw holes (3.0245 N each)


Fig 4 (Left) . Fixed Geometry at Servo Hole and Cylindrical Face Hinge Supports Constraining

Radial and Axial Translation

Fig 5 (Right). Bearing Loads on Bracket Screw Holes w/ ¼ of total applied load at each


Results

Fig 6. Load Case 01 Stress Plot (Left) and Deformation Plot (Right) of 5052-H32 Al Bracket

Fig 7 . Load Case 01 Stress Plot (Left) and Deformation Plot (Right) of 6061-T6 Al Bracket

Fig 8. Load Case 01 Stress Plot (Left) and Deformation Plot (Right) of ABS Plastic Bracket

Material | Max von Mises Stress (MPa) | % of Yield Stress | Max Resultant Deformation (mm)
ABS Plastic | 1.676 | 12.9% | 0.023189
5052-H32 Aluminum | 1.630 | 0.84% | 0.000658
6061 Aluminum | 1.675 | 0.61% | 0.000669

Fig 9. Table of Results from Static FEA Analysis

The results of the static analysis show that ABS plastic, despite having the lowest yield

strength out of the three material options, only demonstrates a maximum resultant stress of 1.676

MPa, which is is 12.9% of the material yield strength. Elastic deformation using ABS plastic is

negligible, totally to 0.023 mm of resultant displacement. 5052 and 6061 Aluminum both

exhibited lower maximum resultant stresses than ABS plastic, however, ABS plastic still exceeds

the functional requirements set forth for the part. When considering costs alongside these results,

ABS plastic becomes the clear best option for manufacturing when considering applied stresses

and cost.

The final consideration to satisfy the functional requirements is the ability to hold the

screws needed to mount the servo. Case studies conducted on plastic components interfacing

with metal fasteners have demonstrated failure on the plastic components as a result of abrasion

via the metal fasteners. However, Anteater Dynamics is aiming to provide a mid-range option,

not a high-end robotic arm that would price out average consumers. While there is risk of failure

in a plastic bracket, solutions such as metal washers and spacers have been proven to increase the

lifecycle of plastic components that interface with metal fasteners. The washers and spacers,

when applied to all points of fastener contact, help distributed the load and prevent the fastener

from acting on the plastic components.

In conclusion, through this analysis it is clear that ABS plastic utilized through additive

manufacturing techniques such as 3D printing or injection molding is the material best suited for

manufacturing the wrist bracket component for Anteater Dynamics’ Robotic Arm. While the

plastic may face earlier failure due to fastener abrasion, the satisfactory strength and considerable

cost savings along with the implementation of washers and spacers makes ABS plastic the

superior material.

Appendix

Ref-1) MatWeb - Material Property Data, Overview of materials for Acrylonitrile Butadiene

Styrene (ABS), Extruded,

https://www.matweb.com/search/datasheet.aspx?MatGUID=3a8afcddac864d4b8f58d40570d2e5

aa&ckck=1 (https://www.matweb.com/search/datasheet.aspx?MatGUID=3a8afcddac864d4b8f58d40570d2e5aa&ckck=1)

Ref-2) MatWeb - Material Property Data, Aluminum 5052-H32,

https://www.matweb.com/search/datasheet.aspx?MatGUID=96d768abc51e4157a1b8f95856c490

28 (https://www.matweb.com/search/datasheet.aspx?MatGUID=96d768abc51e4157a1b8f95856c49028)

Ref-3) MatWeb - Material Property Data, Aluminum 6061-T6; 6061-T651,

https://www.matweb.com/search/datasheet.aspx?MatGUID=b8d536e0b9b54bd7b69e4124d8f1d

20a (https://www.matweb.com/search/datasheet.aspx?MatGUID=b8d536e0b9b54bd7b69e4124d8f1d20a)

Ref-4) OnlineMetals.com, https://www.onlinemetals.com/en/buy/aluminum

Ref-5) Business Analytiq, Acrylonitrile butadiene styrene (ABS) price index,

https://businessanalytiq.com/procurementanalytics/index/acrylonitrile-butadiene-styrene-abs-usa

-price-index-2/ (https://businessanalytiq.com/procurementanalytics/index/acrylonitrile-butadiene-styrene-abs-usa-price-index-2/)

Ref -6) Plastic-Sheets, ABS Advice, http://www.plastic-sheets.co.uk/product-range/abs-advice/

Ref-7) The Madison Group, CASE STUDIES OF PLASTIC FAILURES ASSOCIATED WITH

METAL FASTENERS,

https://madisongroup.com/wp-content/uploads/2022/09/ANTEC2016JansenPlasticwithMetal-Fas

teners.pdf (https://madisongroup.com/wp-content/uploads/2022/09/ANTEC2016JansenPlasticwithMetal-Fasteners.pdf)

The primary research focused on finding reliable material data for the materials being

considered. When researching, finding websites that met industry standards was an important

part of the process. When researching for evidence regarding failure in plastic components,

initial results yielded mostly help forums with hobbyists looking for advice. Adjusting the search

parameters to specify “case studies” helped yield scholarly articles which would provide reliable

information for analysis.

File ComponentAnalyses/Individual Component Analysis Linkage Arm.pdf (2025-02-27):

## Individual Component Analysis

# Linkage Arm


### Anteater Dynamics – 7DOF Robotic Arm

### Ishan Malik ID 51125660

### Table of Contents

List of Figures | 2
List of Tables | 3
Project Overview and Component Justification | 3
Linkage Functional Requirements | 5
Analysis Methodology | 5
Results and Analysis | 12
References | 16
Appendix A – CAD Drawing of Final Beam | 17

List of Figures

Figure 1 Force Application Location | 5
Figure 2 Force Application Location | 6
Figure 3 Linkage Beyond First Linkage Arm | 6
Figure 4 Center of Mass of Remaining Linkage | 8
Figure 5 Distance Between Center of Mass of Arm Portion and Rotation Axis | 8
Figure 6 Point of Application of 1Nm Torque | 9
Figure 7 Face 1 FEA Result | 10
Figure 8 Face 2 FEA Result | 10
Figure 9 Torsional FEA Results | 11

List of Tables

Project Overview and Component Justification

Anteater Dynamics is working with industry sponsor ROBOTIS to develop a 7 degree of

freedom (DOF) robotic arm to be used for machine learning data collection and by at home robotics

enthusiasts. The arm is to use Robotis’ proprietary Dynamixel-X servos motors for actuation, and

will have a completed bill of materials of roughly $1000. The arm should be easy to assemble, and

any parts that are not purchased like the servos or Robotis’ frames used to join the servos should

be able to be both injection molded or 3D-printed, making the project open source for robotics

enthusiasts.

The robotic arm is a mechanical linkage with a total of 6 servos and 3 links. The Linkage

Arms are the connection from one servo to another in the linkage, and as such, are subject to

dynamic loads imposing both torsional and bending stresses on the linkage arms. To ensure proper

functionality, the Linkage Arms must be strong enough to resist these forces. As such, various

cross sections of these linkage arms are to be analyzed using finite element analysis (FEA)

simulations allowing the optimal cross section to be determined for the application. Cross sections

to be analyzed include typical engineering beam cross-sections (I/H-beam, hollow/solid

rectangular, hollow/solid tubular, channels, etc), along with a few other atypical cross sections.

Beam cross sections, in general, have different advantages and disadvantages depending

on the application. The two main types of stresses the linkage arms will be exposed to are bending moments and torsion. A beam’s resistance to bending moments is related to the amount of cross-

sectional area of the beam and its location from the cross section’s neutral axis - the axis in the

cross section of a beam (a member resisting bending) along which there are no longitudinal stresses

or strains. More mass concentrated further from the neutral axis increases the beams resistance to

bending and as such, H and I beams are often used in situation where bending stresses are present.

However, H and I beams are typically much stronger when a force is applied in one direction than

another, so they are typically used in static scenarios where the load directions are not changing

directions, as they will in the robotic arm. A beam’s resistance to torsional stresses is related more

to the actual geometry of the beam. Typically, shapes that have a closed cross section, such as a

tube, pipe, or rectangle, are more resistant to bending than those that do not, such as the I and H

beam.

For the application in the 7-degree-of-freedom robotic arm, these types of stresses both

need to be accounted for. In general, bending stresses will be more common in this application,

especially in the first linkage arm, as the linkage arm must resist bending from the mass of any

object lifted and the weight of all the links that follow it. The servos themselves will also provide

significant amounts of torque to the linkage arms, meaning that resistance to torsion is also

desirable. Several different shapes will be analyzed to ultimately decide on the final linkage arm

shape. It is important to also ensure that the shape of these linkage arms should be easily

manufactured, via both 3D-printing and injection molding. The goal of this analysis is to find the

linkage arm cross section that best resists bending and torsional deformation, accounting for ease

of assembly and total material usage. The results of the engineering analysis will be analyzed in a

decision matrix to dictate which cross section best suits the application.

Linkage Functional Requirements

FRB-1: The arm linkage shall provide the reach to pick objects at a distance of 500 mm away

FRB-2: The servos in the arm linkage shall support the load of 400 g at the end effector

FRB-3 The arm linkage shall articulate to move around obstructions

Analysis Methodology

For testing, the same forces were applied in a static FEA simulation to six different beam

cross sections. The Linkage Arm was modeled as solid acrylonitrile butadiene styrene (ABS) as

the method of manufacturing desired by the project sponsor is injection molded ABS. A 16

Newton force was applied across the faces shown in figures 1 and 2 with the bottom face of the

linkage arm fixed.


Figure 1 Force Application Location


Figure 2 Force Application Location

The 16 N force was chosen as the weight of the entire linkage that exists beyond the first linkage

arm (see figure 2) arms is roughly 0.400 kg, as estimated from the CAD model of the linkage.

Figure 3 Linkage Beyond First Linkage Arm

Adding a 400 g object that can be grasped by the end effector, the resulting total mass is 0.800

kg. The weight of this entire portion of the arm would then be 0.850kg*9.8m/s² = 7.84 N.

Multiplying by a safety factor of 2 arrives at a 15.68 N force, which was then rounded to 16 N to

represent a worst-case bending scenario experienced by the first linkage arm. The force was

applied over the shown surfaces as opposed to a point force as when initial simulation was

completed the highest deformation point of the component occurred locally at the point of

application, not providing characteristic results for the simulation.

For torsional analysis the largest torsional force that will be applied to the first linkage

will come from the inertial forces stopping the rotation of the entire arm. To simulate this force,

it is assumed that the arm is spinning at 20 RPM at the base, and then decelerates to 0 RPM over

a quarter of a second, resulting in an angular acceleration of -8π/3 rad/s² or -480 deg/s²
. Using

the relationship between torque, moment of inertia, and angular acceleration we can arrive at a

reasonable torque to be applied for this simulation. Principal moment of inertia about center of

mass of the arm remaining after the first linkage (see figure 4) was calculated in SolidWorks to

be Pz = 8327341.62 g*mm²
. Using the parallel axis theorem to translate this moment of inertia

around the centroid to the axis of rotation for the arm (I=Io+Md²
), located roughly 270mm from

the linkage centroid, we arrive at the moment of inertia of this remaining portion of the linkage

about its axis of rotation of ~37487341 g*mm² = 0.0375 kg*m² (see figures 4 and 5 for

reference).


Figure 4 Center of Mass of Remaining Linkage

Figure 5 Distance Between Center of Mass of Arm Portion and Rotation Axis

Since T=I*α from the values calculated above, we arrive at a torque of T = 0.0375*(8π/3) =

0.157 Nm. To include a factor of safety, and for simplicity, torsional simulation was done with a

1 Nm torque applied axially, centered on the top face of the beam (see figure 6 for reference).


Figure 6 Point of Application of 1Nm Torque

Three FEA simulations are to be conducted on each beam cross section: two with 16 N

forces on the two major faces of the beam inducing bending moments, and one with the 1 Nm

torque applied to the top face of the beam. Results are to be analyzed based on the maximum

displacement in each of these three simulations. Results for each of the FEA simulations will then

be compared to deciding the final cross-sectional area for the linkage arm. Results for these three

simulations for a rectangular cross sectioned beam are shown in figures 7, 8, and 9 below.


Figure 7 Face 1 FEA Result

Figure 8 Face 2 FEA Result


Figure 9 Torsional FEA Results

Results and Analysis

Six different beam cross-sections were analyzed. The selected beam cross sections are

shown in table 1 below.


Table 1 Beam Cross Sections

Rectangle

Hollow Rectangle

H/I Beam

Plus

Cylinder

Tube

Beam Cross Section

Table 2 below summarizes the results of the FEA simulations

Beam Cross
Section

Total Cross
Sectional Area
(mm^2)

Max
Displacement
Face 1 (mm)

Max
Displacement
Face 2 (mm)

Max Displacement
Torsion (mm)
Rectangle | 369.14 | 0.108758 | 0.125352 | 0.102243
Hollow Rectangle | 220.50 | 0.141146 | 0.158717 | 0.119934
H/I Beam | 270.14 | 0.123223 | 0.236985 | 0.299817
Plus | 302.14 | 0.223128 | 0.092971 | 0.274458
Cylinder | 314.16 | 0.163073 | 0.162685 | 0.123071
Tube | 201.50 | 0.194030 | 0.193307 | 0.136744

Table 2 FEA Simulation Results

The table shows the maximum displacements caused by the loads described in the previous

section. Ideally, this test would have been able to be conducted with cross sections of the same

total area but differing shapes. This was not possible as the linkage arm shape is constrained by

the mounting holes on ROBOTIS frames.

To decide on a final linkage shape, a weighted decision matrix is used to consider additional

factors beyond just the simulation results. Bending resistance, quantified by max displacement on

face one and face two are weighed the highest, at 25% each. Next torsional resistance, quantified

by maximum displacement in the torsional test, is important, but not to the same level as bending

and as such is weighted at 20%. To consider cost, total cross-sectional area is included in the

decision matrix, weighing 10%. Since the part is to be additively manufactured, all the cross

sections are similar in terms of tooling and manufacturing processes. Therefore, the cost of the part

can be quantified simply by the amount of material necessary to manufacture it – a larger cross-

sectional area requires more material. Finally, ease of assembly is considered as the final factor of

the decision matrix. Ease of assembly is related to how simple routing cables around these various cross sections will be to allow for connection of the servo motors. Hollow cross sections make

cable routes easy, as they provide a channel for cables to run through, removing the need for any

external cable routing clips or other solutions. Proper cable routing solutions significantly

decreases the risk of cables between servos snapping or getting disconnected, and as such, this

category is weighed relatively heavily at 20%. The resulting decision matrix is shown below.

Rating 1 - 6 | | Bending Face 1 | Bending Face 2 | Torsion | Total Cross Section | Ease of Assembly | SCORES
| Category Weight | 25.00% | 25.00% | 20.00% | 10.00% | 20.00% | 100.00%
| Rectangle | Rating | 6 | 5 | 6 | 1 | 2 | 4
| | Weighted Score | 25% | 21% | 20% | 2% | 7% | 74%
| Hollow Rectangle | Rating | 4 | 4 | 5 | 5 | 5 | 4.6
| | Weighted Score | 17% | 17% | 17% | 8% | 17% | 75%
| H/I Beam | Rating | 5 | 1 | 1 | 4 | 3 | 2.8
| | Weighted Score | 21% | 4% | 3% | 7% | 10% | 45%
| Plus | Rating | 1 | 6 | 2 | 3 | 4 | 3.2
| | Weighted Score | 4% | 25% | 7% | 5% | 13% | 54%
| Cylinder | Rating | 3 | 3 | 4 | 2 | 1 | 2.6
| | Weighted Score | 13% | 13% | 13% | 3% | 3% | 45%
| Tube | Rating | 2 | 2 | 3 | 6 | 6 | 3.8
| | Weighted Score | 8% | 8% | 10% | 10% | 20% | 57%

Cross
Section

Table 3 Weighted Decision Matrix

Based on the weighted decision matrix and FEA results, the final cross section of the

beam will be hollow rectangular. Looking at the results outlined in Table 1, we can see that in

this case the beam that performed best is the rectangular beam, but when considering other

factors like ease of assembly and total cross section, the hollow rectangular beam is the best choice. See Appendix A for an engineering drawing that fully specifies the final shape of the

Linkage Arm.

References

YouTube. https://www.youtube.com/watch?v=cgLnADEfm6E. Accessed 26 Feb. 2025.

ASME Y14 | Y14 Standards - ASME. https://www.asme.org/codes-standards/y14-standards.

Accessed 26 Feb. 2025.

Chen, D. H., and K. Masuda. “Rectangular Hollow Section in Bending: Part I – Cross-Sectional

Flattening Deformation.” Thin-Walled Structures, vol. 106, Sept. 2016, pp. 495–507.

ScienceDirect, https://doi.org/10.1016/j.tws.2015.12.019.

Liang, Zoe. Benefits of Different Steel Sections | SkyCiv Engineering. 17 May 2019,

https://skyciv.com/technical/benefits-of-different-steel-sections/.

“Moment of Inertia.” Wikipedia, 7 Feb. 2025. Wikipedia,

https://en.wikipedia.org/w/index.php?title=Moment_of_inertia&oldid=1274383393.

Appendix A – CAD Drawing of Final Beam


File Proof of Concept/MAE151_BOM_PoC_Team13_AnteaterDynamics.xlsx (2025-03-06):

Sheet: BOM End Effector
 | MAE151
 |  | Bill of Materials Template (modified from propelplm.com)
 | PRODUCT NAME | Anteater Dynamics - 7 DoF Robotic Arm
 | DESCRIPTION | End Effector
 | TEAM NUMBER | Team 13
 | TEAM MEMBER NAMES | Lucas Cardona, Ishan Malik, Rogel Aguilar, Diego Avila, Noah Castillo, Tomas Mejia
 | PART COUNT | 68
 | TOTAL COST | $72.94
Level | Item Number | Description | Category | Revision | Quantity | Lifecycle Phase | Notes | Source (shop/distributor) | Distributor Part Num | Cost (ea.) | Cost (tot,) | Link (distributor, g-drive drawing/file, etc)
1 | 10002 | End Effector | MTS | B | 1 | Development | Full Assembly | Custom | - | $0.00 | $0.00
2 | 20002 | DYNAMIXEL XL430-W250-T Servo | OTS |  | 1 | Production | Sponsor's actuator for closing the jaws. | ROBOTIS | 902-0135-000 | $49.90 | $49.90 | https://www.robotis.us/dynamixel-xl430-w250-t/
2 | 20006 | 1kg Strain Guage Load Cell | OTS |  | 2 | Production | Sense force applied to objects. | Amazon | YZC-133 | $6.00 | $12.00 | https://a.co/d/7NPBnNQ
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

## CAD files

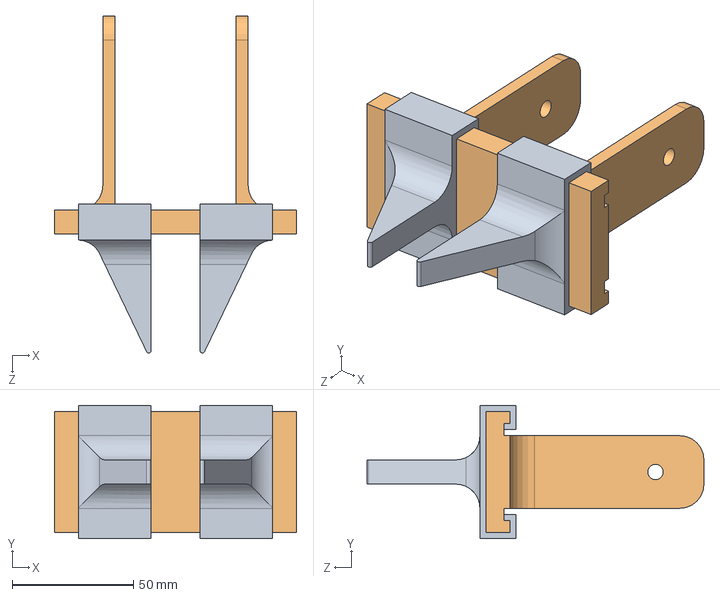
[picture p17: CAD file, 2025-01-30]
Preliminary CAD/Claw_asm.SLDASM
100.0 x 55.0 x 139.1 mm
Claw_track
claw_arm x 2

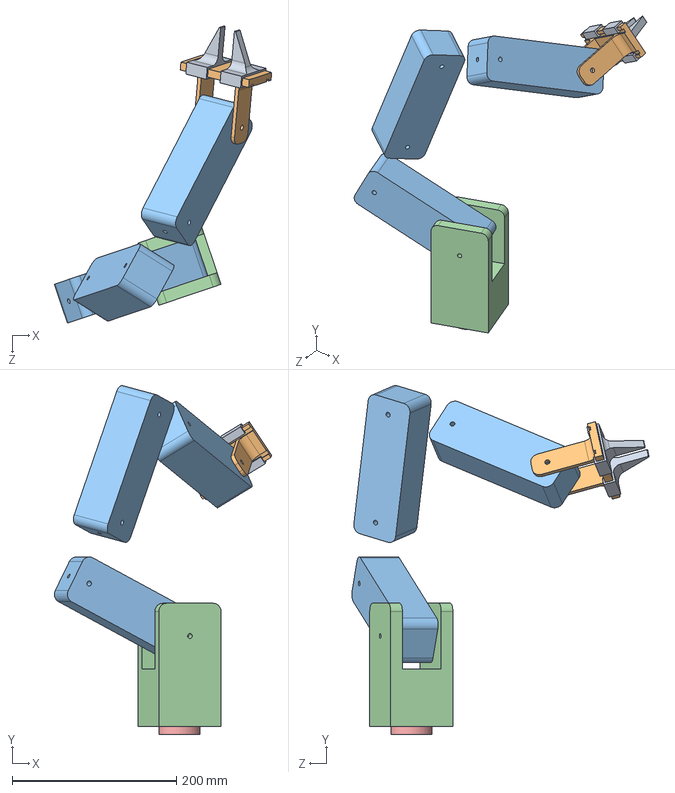
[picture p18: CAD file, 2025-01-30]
Preliminary CAD/.Prelim_arm_asm.SLDASM
265.0 x 425.3 x 362.4 mm
Prelim_Base
Prelim_Link1
Prelim_Link2 x 3
Claw_track
claw_arm x 2

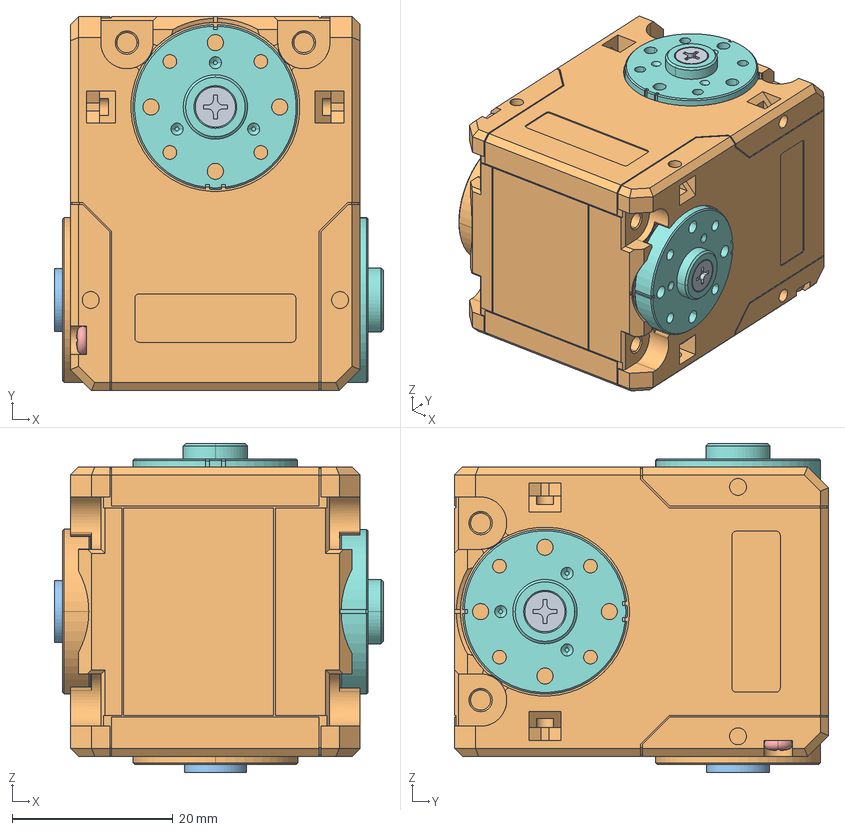
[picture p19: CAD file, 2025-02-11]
RoboticArm_RevD/2XC-430.stp
40.9 x 46.5 x 40.9 mm
DC14_A01_REF
S3B-EH x 2
EHR-3 x 2
PHS_M2X33_TAP_K x 4
DC14_A01_INSERT_2 x 8
DC14_A01_INSERT_1 x 2
DC11_A01_HORN_REF x 2
FHS_M2_5X06_NYLOK x 2
DC11_A01_IDLER_REF x 2
DC11_A01_IDLER_CAP_REF x 2
DC11_A01_IDLER_SCREW x 2

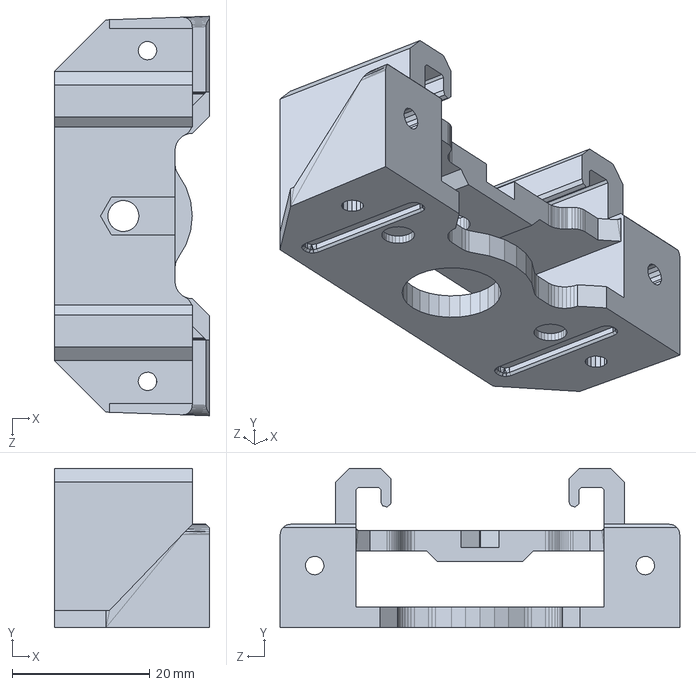
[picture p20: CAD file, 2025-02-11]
RoboticArm_RevD/XL430_EndEffector_RevA/RAIL_BLOCK.SLDPRT
22.5 x 23.1 x 58.0 mm

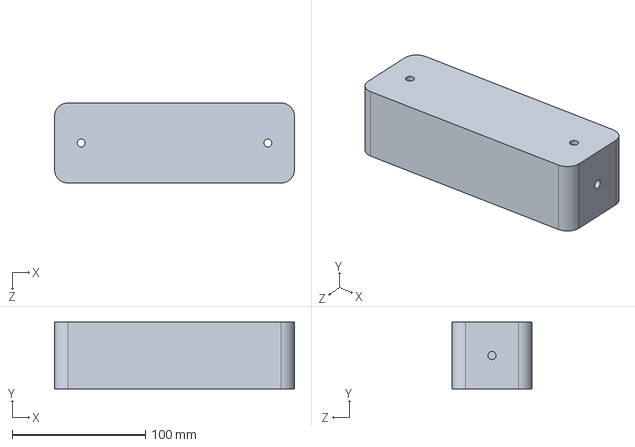
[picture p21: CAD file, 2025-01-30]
Preliminary CAD/Prelim_Link2.SLDPRT
180.0 x 50.0 x 60.0 mm

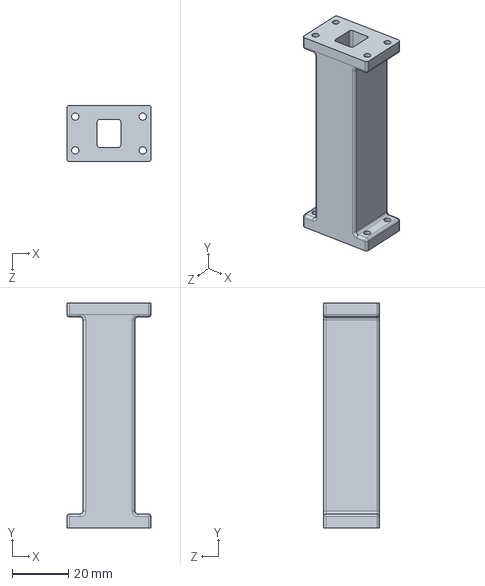
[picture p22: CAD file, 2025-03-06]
Proof of Concept/Linkage/Link1_Hollow_Rectangular.SLDPRT
30.0 x 80.0 x 20.0 mm

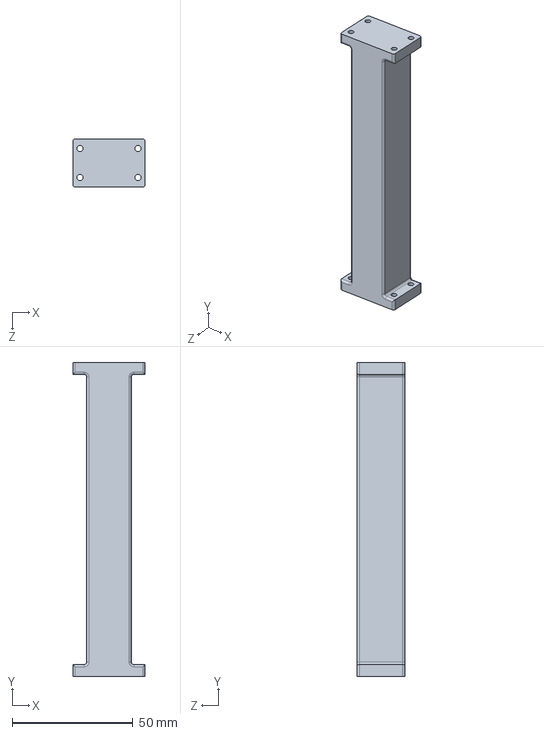
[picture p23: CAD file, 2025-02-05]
RoboticArm_RevD/Link1_revA.SLDPRT
30.0 x 130.0 x 20.0 mm

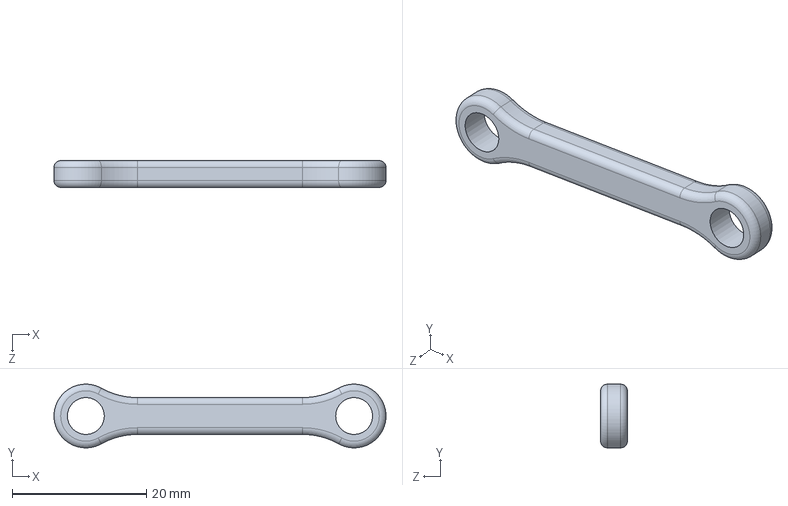
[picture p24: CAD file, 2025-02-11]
RoboticArm_RevD/XL430_EndEffector_RevA/GripperLinkArm.SLDPRT
49.5 x 9.49 x 4.00 mm

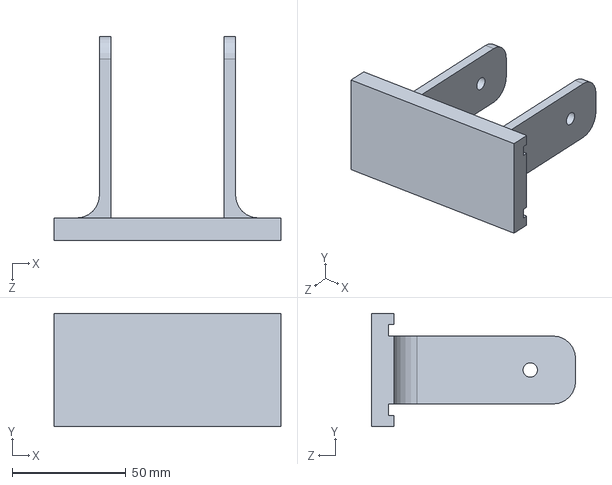
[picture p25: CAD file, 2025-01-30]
Preliminary CAD/Claw_track.SLDPRT
100.0 x 50.0 x 90.0 mm

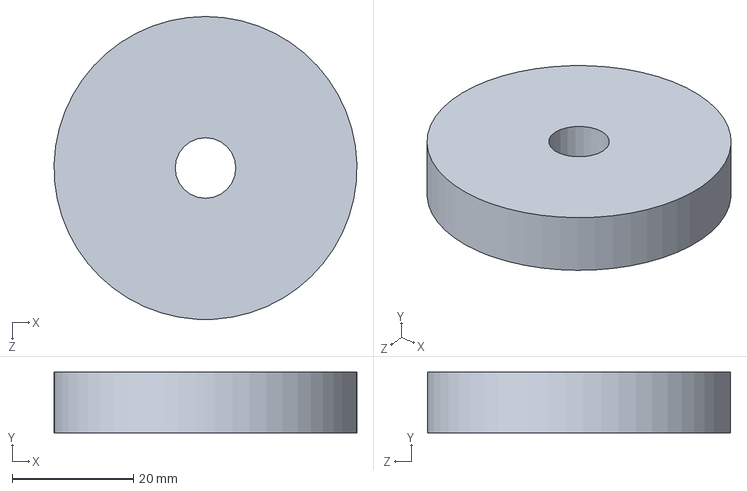
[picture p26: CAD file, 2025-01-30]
RoboticArm_RevD/Prelim_Base.SLDPRT
50.0 x 10.0 x 50.0 mm

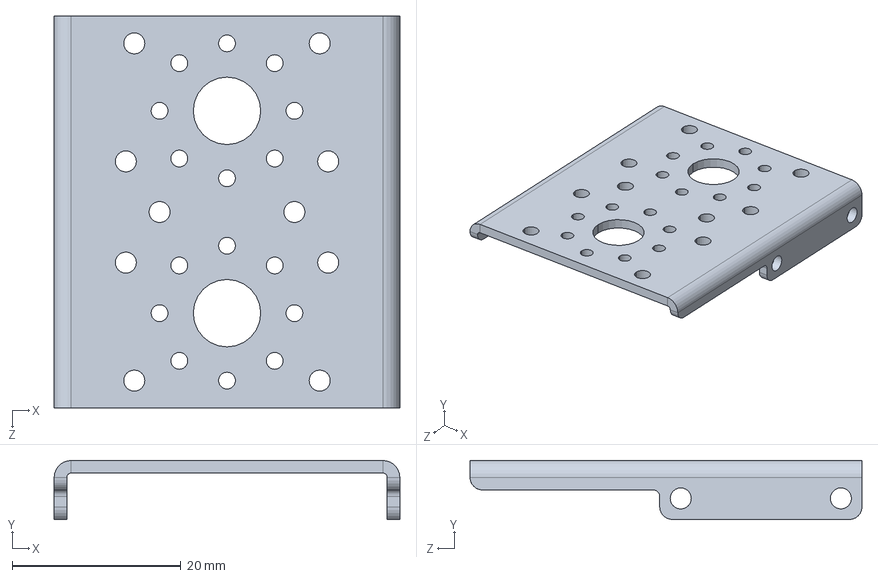
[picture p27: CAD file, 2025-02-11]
RoboticArm_RevD/XL430_EndEffector_RevA/CustomWristFrame01.SLDPRT
41.0 x 7.00 x 46.5 mm

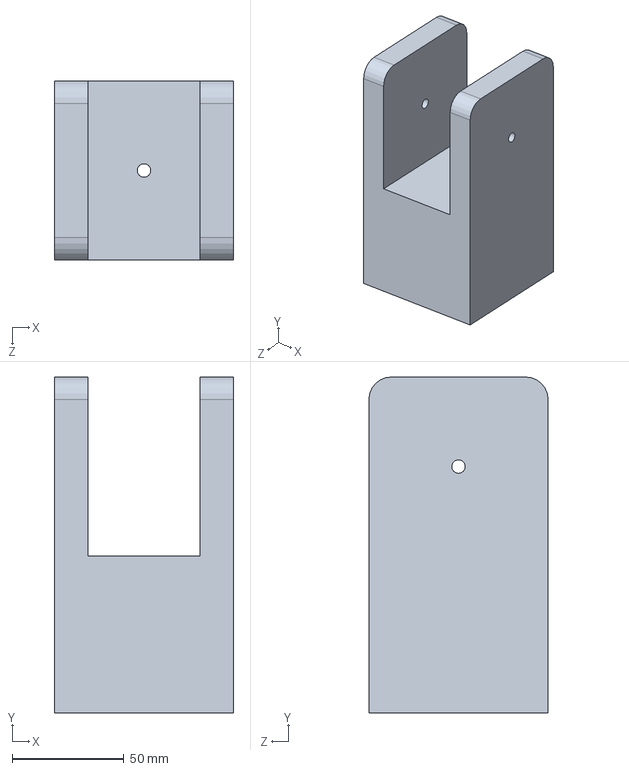
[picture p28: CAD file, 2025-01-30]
Preliminary CAD/Prelim_Link1.SLDPRT
80.0 x 150.0 x 80.0 mm

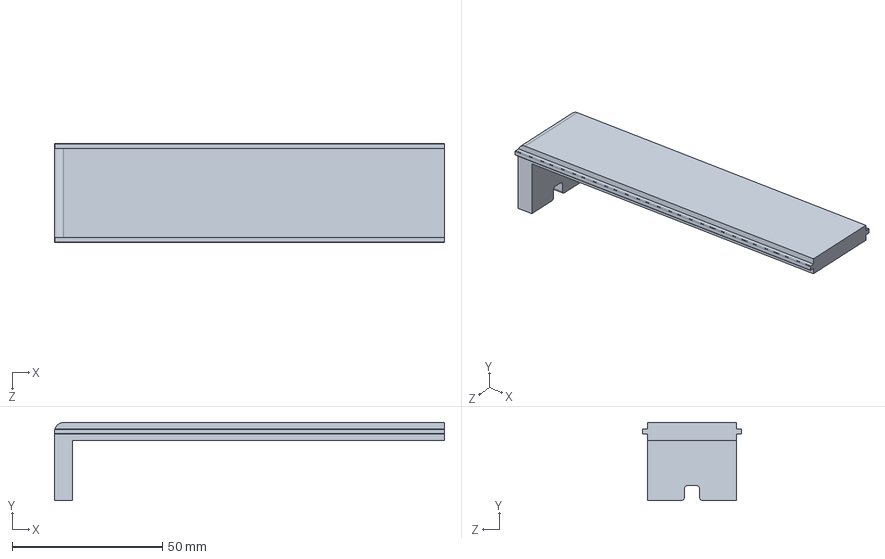
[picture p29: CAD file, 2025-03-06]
Proof of Concept/Linkage/base_elec_cover.SLDPRT
130.0 x 26.0 x 33.1 mm

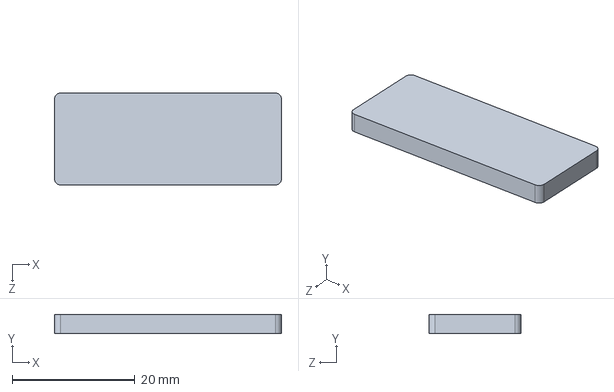
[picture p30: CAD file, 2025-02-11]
RoboticArm_RevD/XL430_EndEffector_RevA/RubberPad.SLDPRT
37.0 x 3.10 x 15.0 mm

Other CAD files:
RoboticArm_RevD/XL430_EndEffector_RevA/XL430 End Effector_RevA.SLDASM
RoboticArm_RevD/XL430_EndEffector_RevA/CustomWristFrame02.SLDPRT
Preliminary CAD/claw_arm.SLDPRT
RoboticArm_RevD/XL430_EndEffector_RevA/RubberPadHolder.SLDPRT
Preliminary CAD/Prelim_Link3.SLDPRT
Proof of Concept/Linkage/90591A270_Zinc-Plated Steel Hex Nut.SLDPRT
Proof of Concept/Linkage/92000A106_Passivated 18-8 Stainless Steel Pan Head Phillips Screws(1).SLDPRT
Proof of Concept/Linkage/92000A107_Passivated 18-8 Stainless Steel Pan Head Phillips Screws.SLDPRT
Proof of Concept/Linkage/93657A202_Nylon Unthreaded Spacer.SLDPRT
Proof of Concept/Linkage/Base_RevA.SLDDRW
Proof of Concept/Linkage/Base_RevA.SLDPRT
Proof of Concept/Linkage/Base_RevA.STL
Proof of Concept/Linkage/Link1_Hollow_Rectangular.STL
Proof of Concept/Linkage/XC-430_idle.SLDASM
Proof of Concept/Linkage/XC-430_idle.stp
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

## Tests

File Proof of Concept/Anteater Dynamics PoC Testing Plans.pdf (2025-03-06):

Anteater Dynamics Robotic Arm Proof of Concept Test Procedures

Rev NC
3/5/25

Introduction

The purpose of the test is to isolate the two primary systems of the robotic arm, the linkages and

the end-effector, and verify that both systems can actuate as designed given specific code input. The test

is designed to not require extra components to be designed, as all tests are conducted using a proof of

concept model that will be incorporated into the final product.

The proof of concept model does not exhibit the full seven degrees of freedom and is rather

limited to four degrees of freedom to simplify software requirements while verifying that the servos can

actuate consecutively to achieve desired movement. The end effector is evaluated separately from the

linkage as its own assembly to eliminate any load from the linkage when conducting tests to calibrate

and tune kinematic software.

The results from the test will be used to inform any revisions to the robot programming which

may be needed and to demonstrate viability of the bespoke end-effector design.

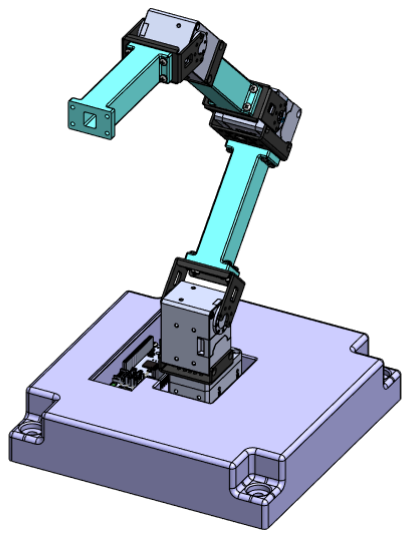
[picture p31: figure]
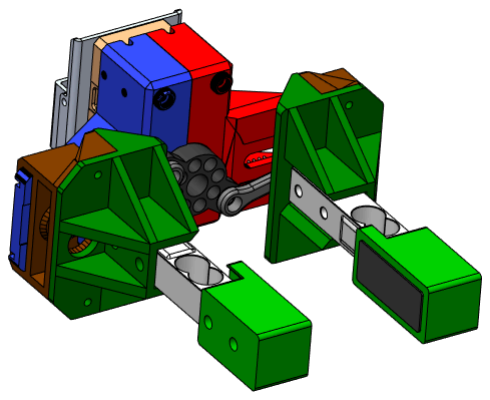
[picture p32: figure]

Fig 1. CAD Models of Four Degree of Freedom Linkage PoC (Left) and End-Effector Assembly Poc (Right)

Test Items

Functional Requirements

(A) Base Actuator

FRA-1: The base actuator shall rotate 360 degrees without binding

FRA-2: The base shall provide a stable and secure mounting platform capable of supporting the

linkage throughout movement

(B) Arm Linkage

FRB-3: The arm linkage shall articulate as dictated by software input

(C) End Effector

FRC-1: The end effector shall pick up small household objects

FRC-2: The end effector shall sense gripping forces

Ref: Preliminary Design Review Presentation Slide 9

Design/Assembly Specifications
- Manufactured parts exhibit the correct desired fits when assembled without interference
- All hardware is compatible and screws exhibit the correct fit for the specified holes

Features to Be Tested

This section and the following offer a high level user overview of features to be tested (and not to be tested in the following section) and assigns perceived risk levels to each respective feature. Feature risk level indicates the importance to the function of the final product and anticipated challenges with implementation. Features given a low risk level have been excluded from the test.

Features | Risk Level
Base Stability | Medium
End Effector Actuation | Medium
Load Cell Force Output | High
Servo Articulation | Medium
Servo Kinematic Rigidity | High

Features Not to Be Tested

Features | Risk Level
Linkage Arm and Bracket Rigidity | Low
End Effector Load Capacity | Low
7 DoF Movement | Low

Linkage and bracket rigidity is described as low risk due to existing validation through static finite element analysis. Simulation results show load bearing capacities of both the linkage arms and brackets exceeds the maximum potential load, including a load factor of 2, by several orders of magnitude.

The end effector load capacity has not undergone prior evaluation, however the robotic arm can operate and demonstrate usefulness even if full load capacity is not achieved. In addition, load capacity of the end effector depends on the servo rigidity of a full linkage, and cannot be fully characterized by the existing proof of concept model.

The proof of concept model used for testing only exhibits four degrees of freedom in linkage arm movement, rather than the full seven degrees of freedom. The integration risk of adding the remaining three degrees of freedom is low, as a test validating the efficacy of four degrees of freedom will also serve to validate the potential for extra mobility.

Test Equipment

Item No. | Quantity | Item name | Unit Price | Total Price
2.1 | 2 | DYNAMIXEL XC430-T240BB-T | $119.90 | $239.80
2.2 | 2 | DYNAMIXEL XL430-W250-T | $49.90 | $99.80
2.3 | 1 | DYNAMIXEL 2XL430-W250-T | $129.90 | $129.90
2.4 | 1 | DYNAMIXEL XM430-W350-T | $269.90 | $269.90
2.5 | 1 | OpenRB-150 Embedded Controller | $24.90 | $24.90
3.1 | 2 | FR12-S102K Set | $19.00 | $38.00
3.2 | 4 | FR12-H101K Set | $40.60 | $162.40
3.3 | 1 | FR12-S101K Set | $28.60 | $28.60
3.4 | 1 | Custom Frame 02 | | $0.00
3.5 | 1 | Custom Frame 01 | | $0.00
1.0 | 3 | Linkage Arms | | $0.00
1.1 | 1 | End Effector Plastic Set (OpenX) | | $0.00
1.2 | 2 | Custom Load Cell Holder | | $0.00
1.3 | 2 | Custom Pad Holder | | $0.00
1.4 | 2 | 1kg Load Cell (YZC-133) + Amp | $4.79 | $9.58

Fig 2. BOM for Proof of Concept Assemblies

Other Test Materials:

- Laptop w/ Arduino IDE
- USB cable
- Stopwatch
- Measuring tape
- Stress Ball
- Wood block

Procedures

L-T1 Rotational Verification (FRA-1)

This test validates the robot’s ability to actuate rotational movement about its central axis. Base stability, servo rigidity, and software integration are analyzed through the test results.

1. Connect Linkage PoC to laptop via USB to OpenRB-150 Controller
2. Load software for test L-T1.1 in Arduino IDE and execute code
a. Code shall direct linkage PoC to rotate the base XC-430 servo 360 degrees while maintaining the first linkage in the upright position
3. Designated tester shall record the time from when the code is ran to the completion of one full rotation of the XC-430 servo using a stopwatch
4. Repeat Step 3 five times and record. Note PoC ability to execute code as desired.
5. Load software for test L-T1.2 in Arduino IDE and execute code
a. Code should direct linkage PoC to rotate the base XC-430 servo 360 degrees while maintaining the first linkage at an angle 30 degrees from normal
6. Designated tester shall record the time from when the code is ran to the completion of one full rotation of the XC-430 servo using a stopwatch
7. Repeat Step 6 five times and record. Note PoC ability to execute code as desired.

L-T2 Linkage Extension (FRB-3)

This test validates the robot’s ability to exhibit kinematic motion actuating all servos rotating about the X and Y axes. Base stability, servo rigidity, and software integration are analyzed through the test results.

1. Connect Linkage PoC to laptop via USB to OpenRB-150 Controller
2. Load software for test L-T2.1 in Arduino IDE and execute code
a. Code shall direct linkage PoC to navigate to starting position where linkage one is normal to the base, linkage two is normal to linkage one, and linkage three is normal to linkage two
b. From starting position, linkage PoC shall sequentially extend linkage three colinear to linkage two, extend linkage two colinear to linkage one, rotate linkage one parallel to base, hold position
3. Designated tester shall record the time from when the code is run to the completion of one full trial using a stopwatch. Verify linkage parallelism and servo rigidity using calipers to measure distance between linkage arm and testing surface at center of each linkage arm.
4. Repeat Step 3 five times and record. Note PoC ability to execute code as desired.

EE-T1 End Effector Grip (FRC-1, FRC-2)

This test validates the robot’s ability to grab objects using the end-effector and receive load feedback through the load cells. Load cell integration, gripper ability, end-effector mechanics, and software integration are analyzed through the test results.

1. Connect End Effector PoC to laptop via USB to OpenRB-150 Controller
2. Load software for test EE-T1.1 in Arduino IDE and execute code
a. Code shall direct end-effector PoC to starting positions with clamps fully opened. Code shall actuate end effector to close clamps around object, returning load cell feedback on applied force in Newtons. When load cell feedback stabilizes, code shall dictate end-effector servo to stop movement and hold the position for 30 seconds.
3. Place deformable stress ball in between end-effector PoC clamps
4. Execute code and record load cell feedback using Arduino IDE
5. Repeat steps 3-4 five times, returning stress ball to original position before each test
6. Place wooden cube in between end-effector PoC clamps
7. Execute code and record load cell feedback using Arduino IDE
8. Repeat steps 6-7 five times, returning stress ball to original position before each test

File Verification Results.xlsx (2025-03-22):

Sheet: Compliance Table
Functional Requirement | Technical Specification | Compliant (C) / Non Compliant (NC)
FRA | Base Actuation Performance
FRA-1 | The base actuator shall rotate to pick up objects all 360 degrees around it | C
FRA-2 | The base shall provide a stable and secure mounting platform for the arm linkage | C
FRB | Arm Linkage Performance
FRB-1 | The servos in the arm linkage shall support the load of 400g at the end effector | C
FRB-2 | The arm linkage shall articulate to move around obstructions | NC
FRC | End-Effector Performance
FRC-1 | The end effector shall pick up small household objects | C
FRC-2 | The end effector shall sense gripping forces | C

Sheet: Rotational Verification (FRA-1)
Trial | Executes Code? Y/N
1 | Y
2 | Y
3 | Y
4 | Y
5 | Y

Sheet: Extension Verfication (FRB-3)
Trial | Distance (Start, mm) | Distance (End, mm)
0g | 63.5 | 63.7
100g - 1 | 63.3 | 63.4
100g - 2 | 63.5 | 62.9
100g - 3 | 63.5 | 62.7
200g - 1 | 63.1 | 62.1
200g - 2 | 63.3 | 62.1
200g - 3 | 63.4 | 62.0

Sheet: Gripper Verfication (FRC-1, FRC
Trial | Average Force Read (N) | Holds Object? Y/N
Soft - 1 | 10.8 | Y
Soft - 2 | 11.97 | Y
Soft - 3 | 12.35 | Y
Hard - 1 | 13.57 | Y
Hard - 2 | 14.8 | Y
Hard - 3 | 12.68 | Y

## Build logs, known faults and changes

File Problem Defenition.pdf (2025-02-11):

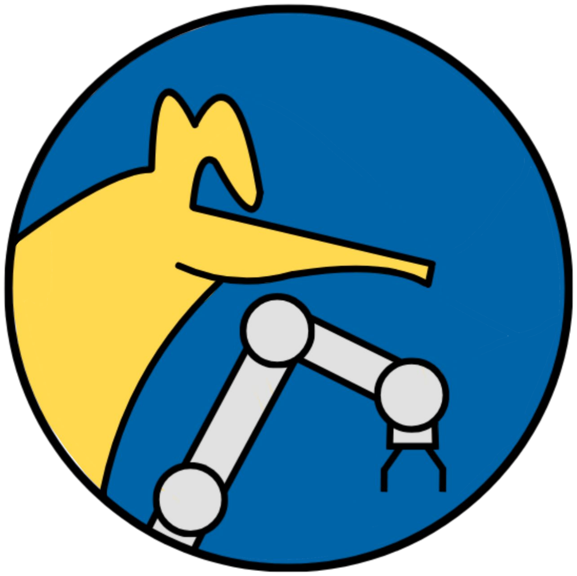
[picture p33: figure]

# Anteater Dynamics

# Problem Definition

# Team Introduction

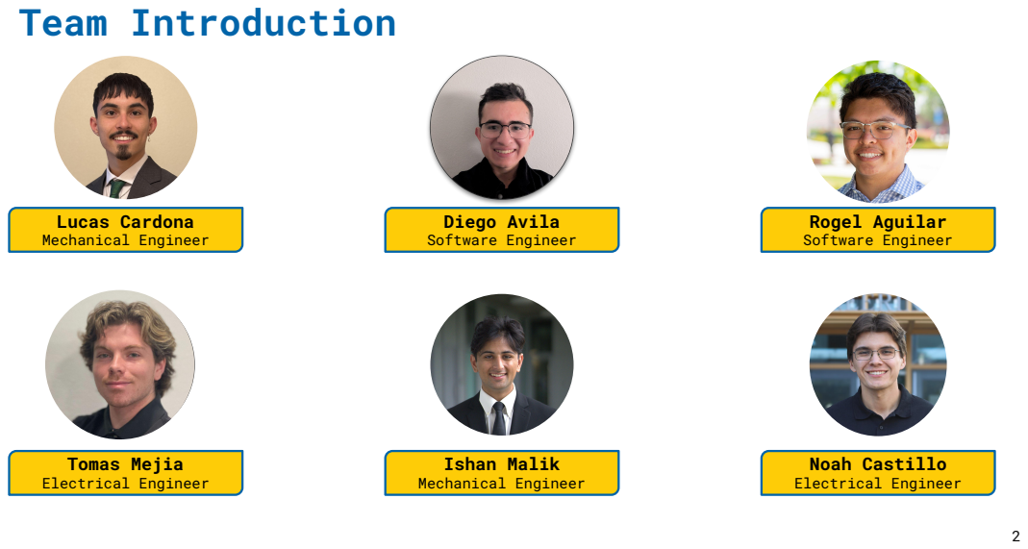
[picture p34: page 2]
Lucas Cardona Mechanical Engineer; Diego Avila Software Engineer; Rogel Aguilar Software Engineer; Tomas Mejia Electrical Engineer; Ishan Malik Mechanical Engineer; Noah Castillo Electrical Engineer

# Quad Chart

Purpose

- Offer mid-tier option robotic arm option for home researchers
- Use to train robotic AI models on interactions with physical world

Customers/Stakeholders

- Industry Sponsor: Robotis Inc
- Open-source design
- For robotics machine learning researchers

Technical Approach

- Incorporate Robotis electronics (sensors, actuators, etc)
- Design parts for additive manufacturing
- Design for ease-of-assembly

Success Criteria

- Able to be mass produced via injection molding OR by 3D printing at home
- $500-$600 full BOM range
- 7DOF for ML research
- Able to pick up ~500g

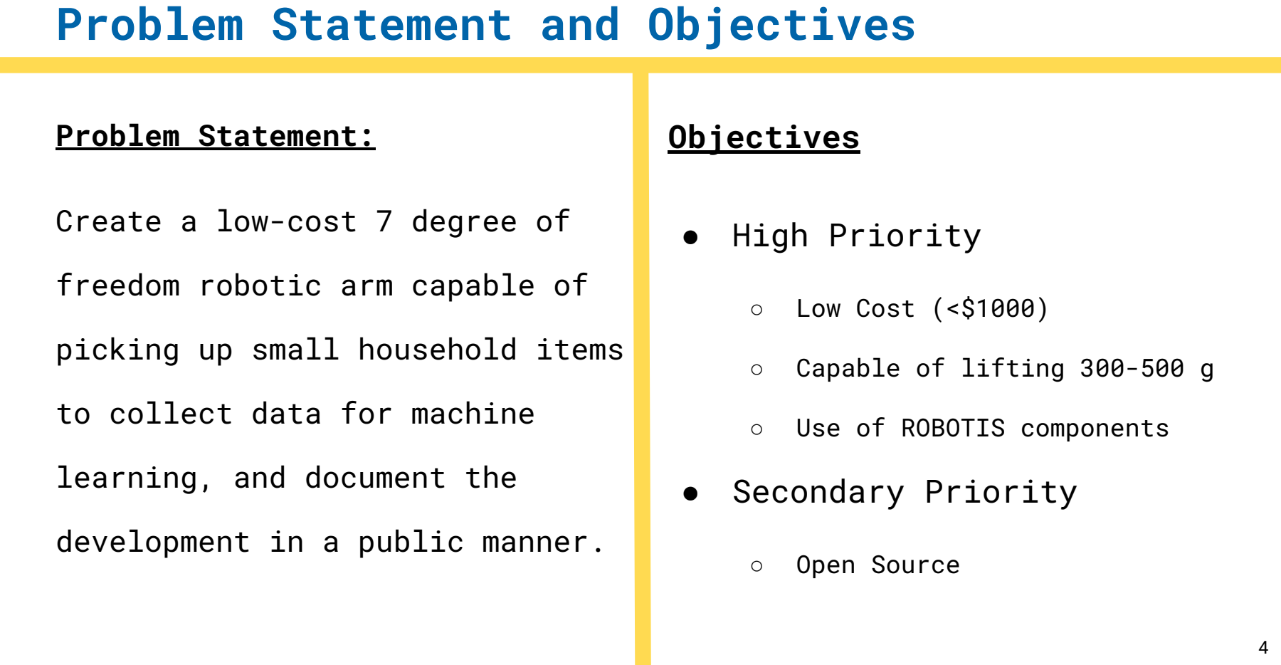
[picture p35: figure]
Problem Statement and Objectives; Problem Statement:; Create a low-cost 7 degree of; freedom robotic arm capable of; picking up small household items; to collect data for machine; learning, and document the; development in a public manner.; Objectives; ● High Priority; ○ Low Cost (<$1000); ○ Capable of lifting 300-500 g; ○ Use of ROBOTIS components ● Secondary Priority; ○ Open Source

# Sponsor & Existing Solutions

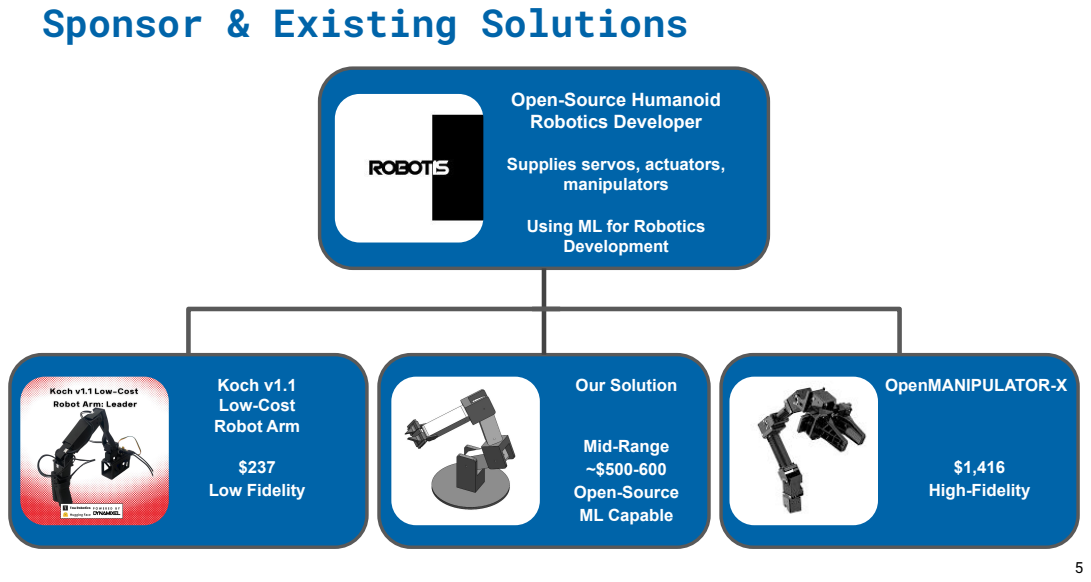
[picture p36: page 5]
OpenMANIPULATOR-X; $1,416 High-Fidelity; Koch v1.1 Low-Cost Robot Arm; $237 Low Fidelity; manipulators; Our Solution; Mid-Range ~$500-600 Open-Source ML Capable

Open-Source Humanoid
Robotics Developer

Supplies servos, actuators,

Using ML for Robotics
Development

# Timeline Milestones

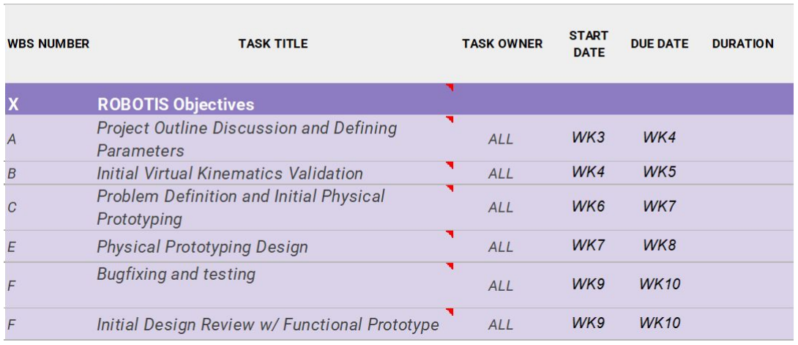
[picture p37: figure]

# Project Deliverables

## 1. 7 DOF Robot Arm

## 2. Project documentation/resources

## 3. Weekly updates on GITHub

# System Requirements

## - 7 DOF - Pick up small household objects (e.g. a soda can) - 650mm reach, 500mm at load - Clamped/Bolted for table mounting - 400g lifting capacity - Aluminum and plastic injection molding - Under $1000

# Measures of Effectiveness

## - The final product is affordable in the $500-600 range - The arm can easily manipulate a 500g mass - The design is open source and available to 3D print at home - Integrates ROBOTIS actuators

# Functional Hierarchy

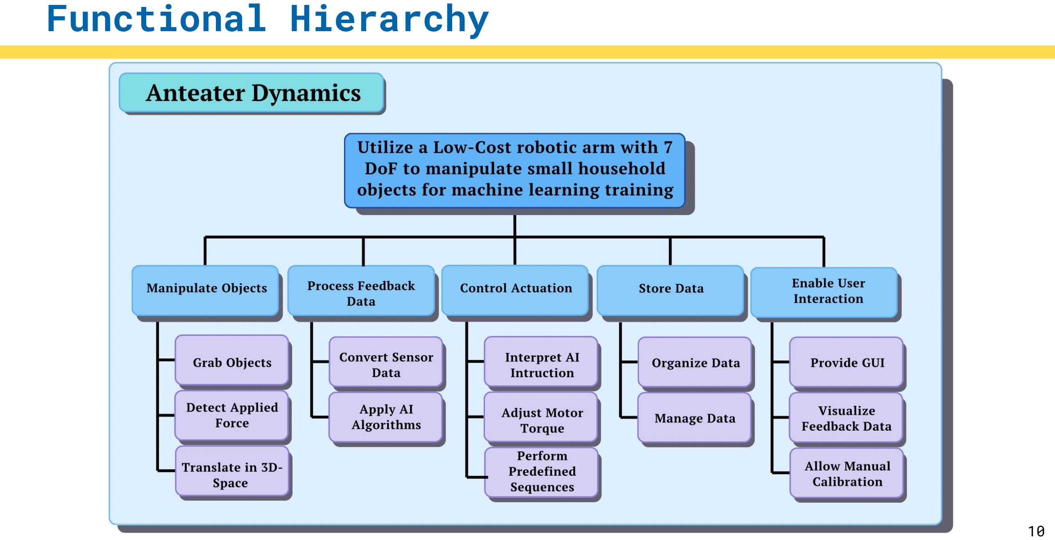
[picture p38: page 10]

# Grey Box Diagram

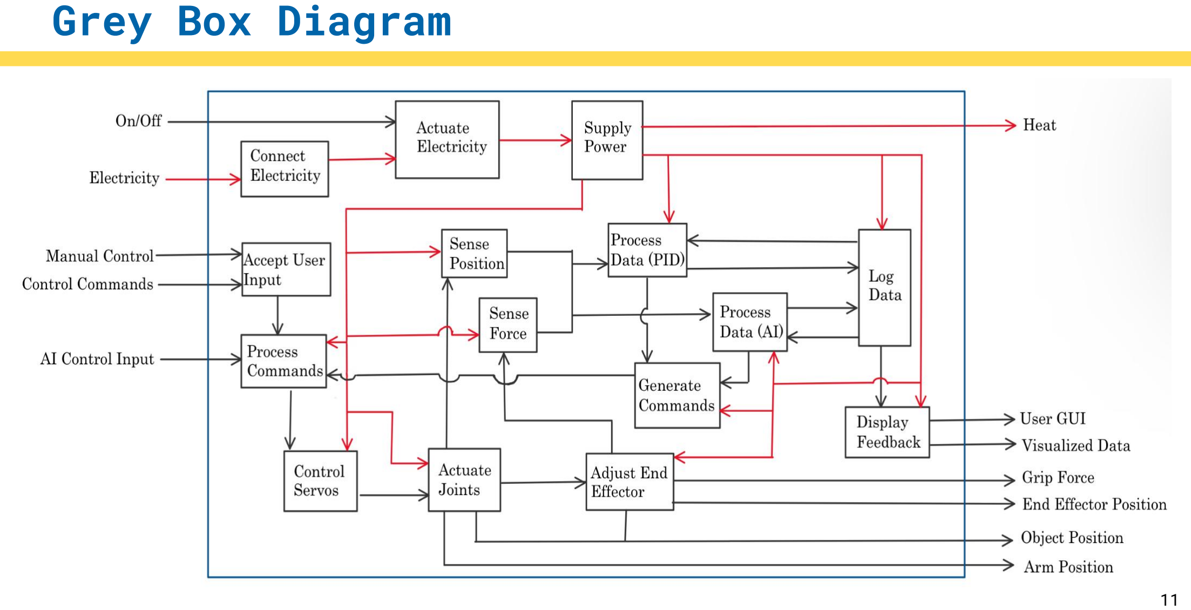
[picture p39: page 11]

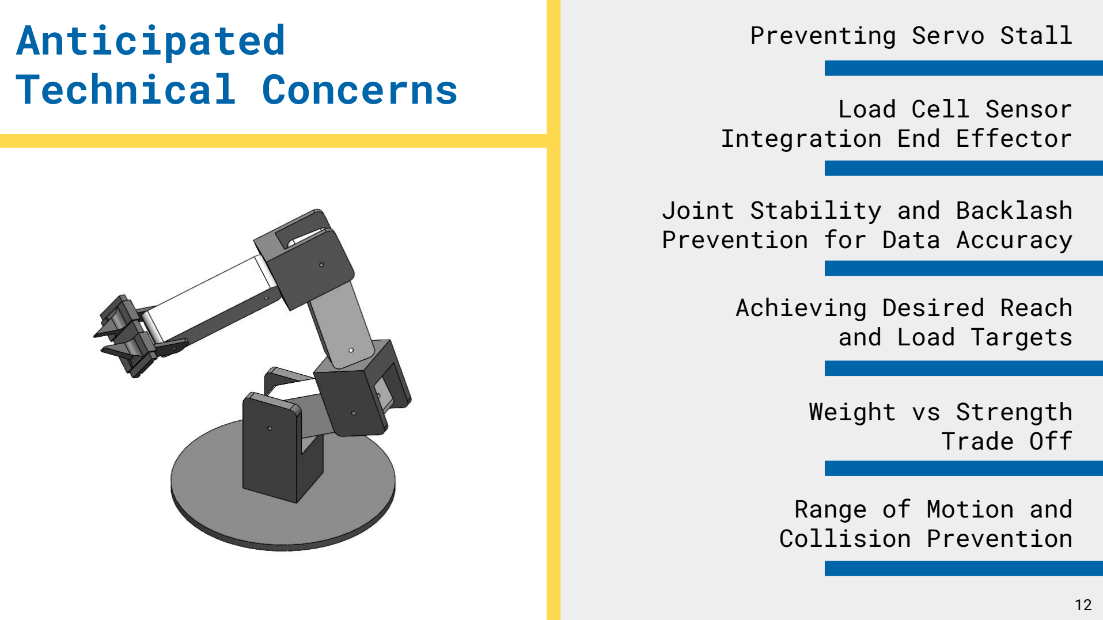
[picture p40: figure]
Anticipated Technical Concerns; Preventing Servo Stall; Achieving Desired Reach and Load Targets; Weight vs Strength Trade Off; Joint Stability and Backlash Prevention for Data Accuracy; Range of Motion and Collision Prevention; Load Cell Sensor Integration End Effector

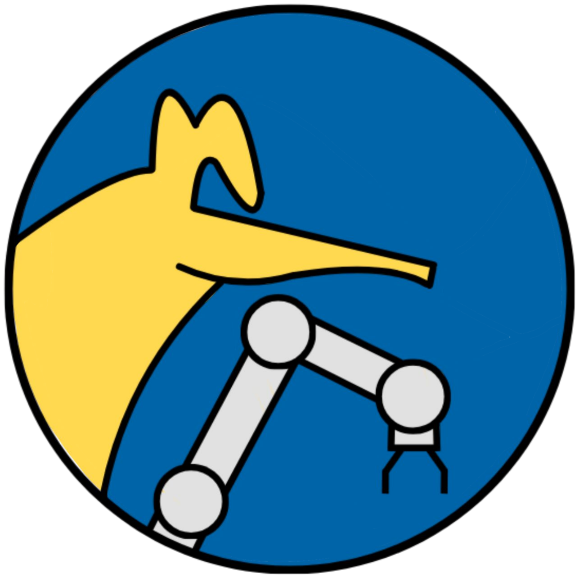
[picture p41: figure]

# Thank You For Listening

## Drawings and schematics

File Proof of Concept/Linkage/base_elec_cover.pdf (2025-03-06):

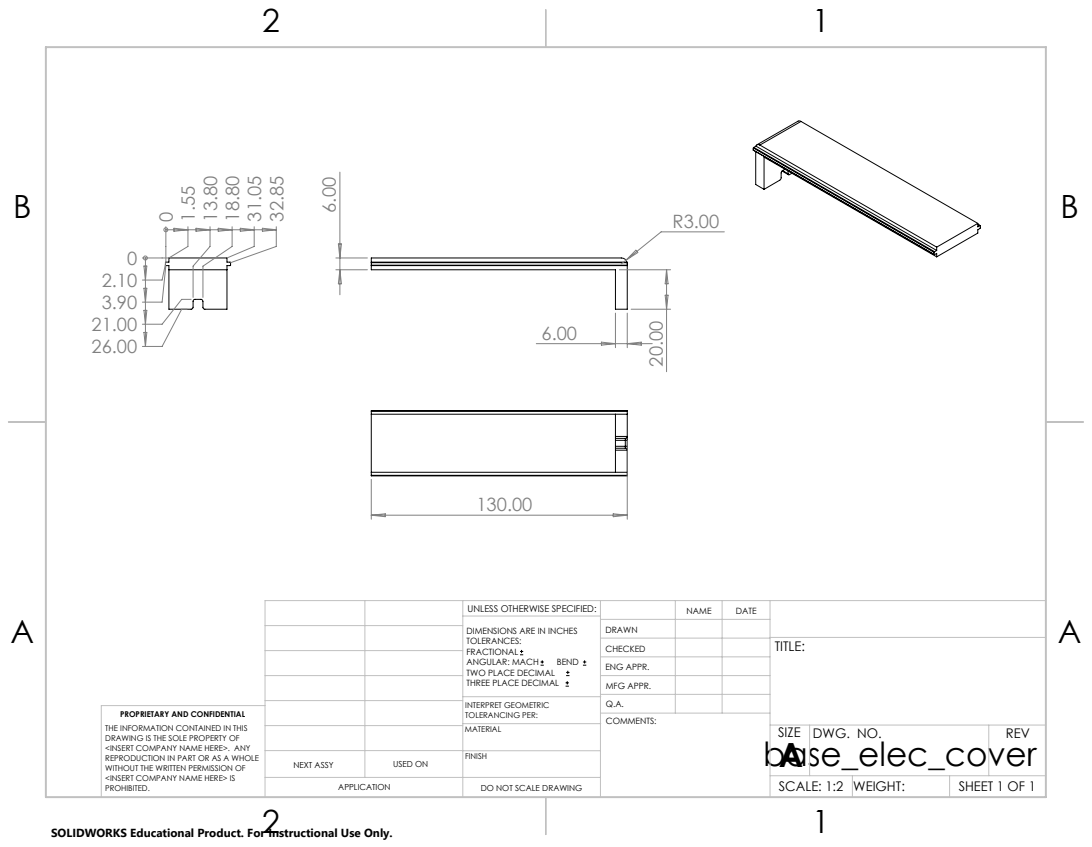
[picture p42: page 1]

UNLESS OTHERWISE SPECIFIED: | | NAME | DATE
DIMENSIONS ARE IN INCHES TOLERANCES: FRACTIONAL ANGULAR: MACH BEND TWO PLACE DECIMAL THREE PLACE DECIMAL | DRAWN

CHECKED | | | TITLE:

ENG APPR.
MFG APPR.

INTERPRET GEOMETRIC TOLERANCING PER: | Q.A.
MATERIAL | base_elec_cover | SIZE A | DWG. NO. | REV

PROPRIETARY AND CONFIDENTIAL
THE INFORMATION CONTAINED IN THIS
DRAWING IS THE SOLE PROPERTY OF
<INSERT COMPANY NAME HERE>. ANY
REPRODUCTION IN PART OR AS A WHOLE
WITHOUT THE WRITTEN PERMISSION OF
<INSERT COMPANY NAME HERE> IS
PROHIBITED.

NEXT ASSY | USED ON | FINISH

APPLICATION | DO NOT SCALE DRAWING | | SCALE: 1:2 | WEIGHT: | SHEET 1 OF 1

SOLIDWORKS Educational Product. For Instructional Use Only.

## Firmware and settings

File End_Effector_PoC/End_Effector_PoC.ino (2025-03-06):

#include <Dynamixel2Arduino.h>
#include <Adafruit_HX711.h>

// OpenRB-150 has DYNAMIXEL TTL bus on Serial2
#define DXL_SERIAL   Serial2
#define DEBUG_SERIAL Serial
const uint8_t DXL_DIR_PIN = -1; // OpenRB-150 doesn't need a DIR pin

const uint8_t DXL_ID = 1;
const float DXL_PROTOCOL_VERSION = 2.0;

Dynamixel2Arduino dxl(DXL_SERIAL, DXL_DIR_PIN);

using namespace ControlTableItem;

// Adafruit HX711 setup for two load cells
const int LOADCELL1_DOUT_PIN = 2;
const int LOADCELL1_SCK_PIN = 3;
const int LOADCELL2_DOUT_PIN = 4;
const int LOADCELL2_SCK_PIN = 5;
Adafruit_HX711 scale1;
Adafruit_HX711 scale2;

// Define safe servo range to avoid mechanical overextension
const int32_t safeMinPosition = 0;    // Minimum safe position (Use degrees)
const int32_t safeMaxPosition = 170; // Maximum safe position (Use degrees)

// Define gripper geometry constants for reference (if needed)
const float maxOpening = 47.0;  // mm: maximum gripper opening at full range

// Force threshold for stopping the gripper (adjust as needed)
const float forceThreshold = 370.0; //In grams Example threshold, adjust based on your load cell

void setup() {
  DEBUG_SERIAL.begin(115200);
  dxl.begin(1000000); // OpenRB-150 uses 1Mbps by default
  dxl.setPortProtocolVersion(DXL_PROTOCOL_VERSION);
  dxl.ping(DXL_ID);

  // Turn off torque when configuring
  dxl.torqueOff(DXL_ID);
  dxl.setOperatingMode(DXL_ID, OP_POSITION);
  dxl.torqueOn(DXL_ID);

  // Adafruit HX711 setup
  scale.begin(LOADCELL_DOUT_PIN, LOADCELL_SCK_PIN);
  if (!scale.is_ready()) {
    DEBUG_SERIAL.println("HX711 not found.");
    while (1);
  }
  scale.set_scale(); // Set scale if you have a known calibration factor
  scale.tare();      // Reset the scale to 0

  // Set up potentiometer pin
  pinMode(D15, INPUT);//Not sure if this is the right pin-number
}

void loop() {
  // Read the potentiometer value (0 to 1023)
  int potValue = analogRead(D15);

  // Map the potentiometer value to the safe position range
  int32_t targetPosition = map(potValue, 0, 1023, safeMinPosition, safeMaxPosition);

  // Read the current position
  int32_t currentPosition = dxl.getPresentPosition(DXL_ID, UNIT_DEGREE);

  // Read force from load cell
  float force = scale.get_units();

  // Move the gripper if force is below threshold
  if (force < forceThreshold) {
    dxl.setGoalPosition(DXL_ID, targetPosition);
  }

  // Calculate the corresponding gripper opening (for debugging)
  float opening_mm = ((currentPosition - safeMinPosition) / float(safeMaxPosition - safeMinPosition)) * maxOpening;

  // Debug output
  DEBUG_SERIAL.print("Potentiometer: ");
  DEBUG_SERIAL.print(potValue);
  DEBUG_SERIAL.print("  ->  Position: ");
  DEBUG_SERIAL.print(currentPosition);
  DEBUG_SERIAL.print("  ->  Opening: ");
  DEBUG_SERIAL.print(opening_mm);
  DEBUG_SERIAL.print(" mm  ->  Force: ");
  DEBUG_SERIAL.print(force);
  DEBUG_SERIAL.println(" units");

  delay(15);  // Small delay for smooth operation
}
